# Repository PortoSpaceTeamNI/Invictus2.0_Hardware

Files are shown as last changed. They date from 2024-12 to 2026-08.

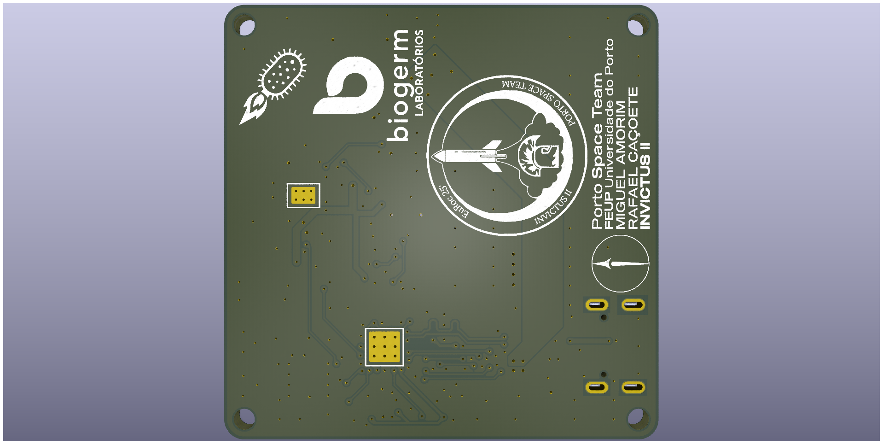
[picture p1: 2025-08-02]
Boards/PayLoad/PocketSat/Renders/PocketSat_Back.png

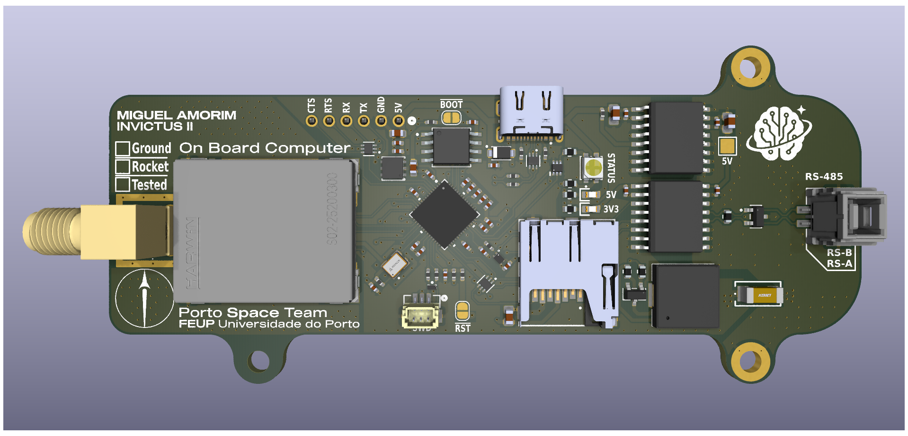
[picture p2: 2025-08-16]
Boards/Rocket Systems/OBC/Renders/OBC_front.png

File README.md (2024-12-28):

Este repositório é usado para gerir as versões dos projetos KiCAD do sistema de Avionics da Porto Space Team.
Está dividido em 2 secções: 
  1. A biblioteca de símbolos, footprints e modelos 3D dos diversos componentes usados no design, cada pasta do símbolo deve apenas incluir os ficheiros de .kicad_sym, .kicad_mod e .step todos juntos apenas dentro de uma única pasta com um nome adequado.
  2. A pasta Boards que contém os diversos ficheiros de schematic (.kicad_sch), pcb (.kicad_pcb) e project (.kicad_pro) de todo o sistema de Avionics.

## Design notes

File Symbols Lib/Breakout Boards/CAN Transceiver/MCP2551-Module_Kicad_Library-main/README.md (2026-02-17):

# MCP2551-Module-3D-model
3D model of the MCP2551 module that can be used for Kicad or any other ECad that use as .step file for rendering the 3D view

## Image

Render Canbus

## Italiano
Questo modello 3D rappresenta il modulo CanBus che sfrutta il chip MCP2551.
È stato creato per poter essere inserito negli schematici di Kicad per poterlo visualizzare nella visualizzazione 3D.
Questo modello è stato utilizzato sopratutto per la creazione delle schede che serviranno a gestire la telemetria del veicolo fatto dal team di Formula Sae dell'Unipg Racing Team

## English
This 3D model represents the CanBus module that uses the MCP2551 chip.
It was created to be inserted into the Kicad schematics to be able to view it in 3D view.
This model was used above all for the creation of the boards that will be used to manage the telemetry of the vehicle made by the Formula Sae team of the Unipg Racing Team

## Contacts 
Personal Instagram: [@marco.dok](https://www.instagram.com/marco.dok/)
Unipg Racing Team: [@unipgracing_team](https://www.instagram.com/unipgracing_team/)

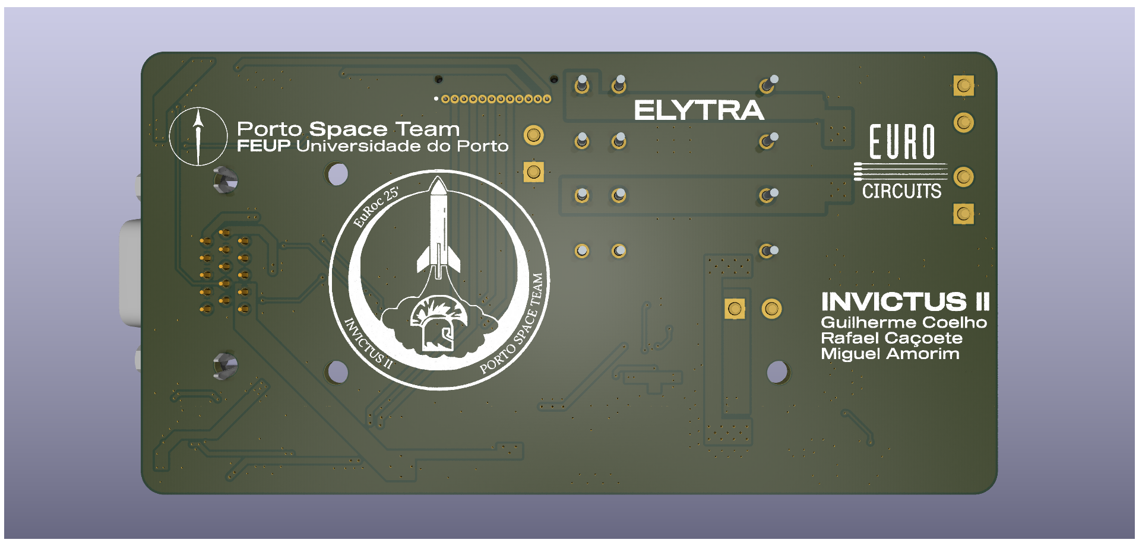
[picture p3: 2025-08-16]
Boards/Rocket Systems/Elytra/Renders/Elytra_back.png

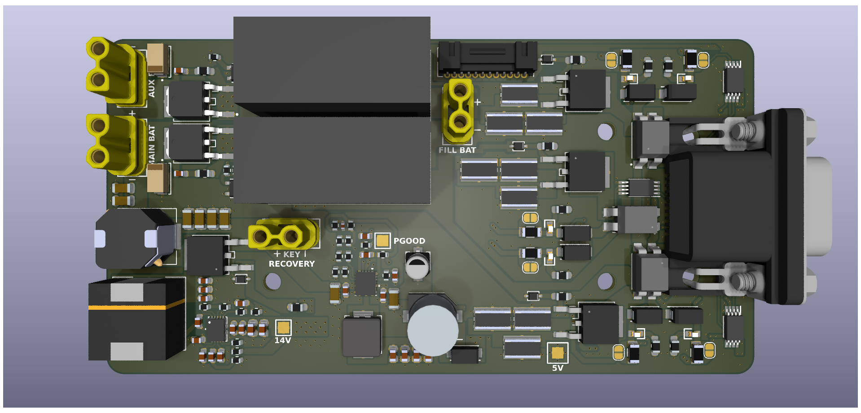
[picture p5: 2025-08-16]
Boards/Rocket Systems/Elytra/Renders/Elytra_front.png

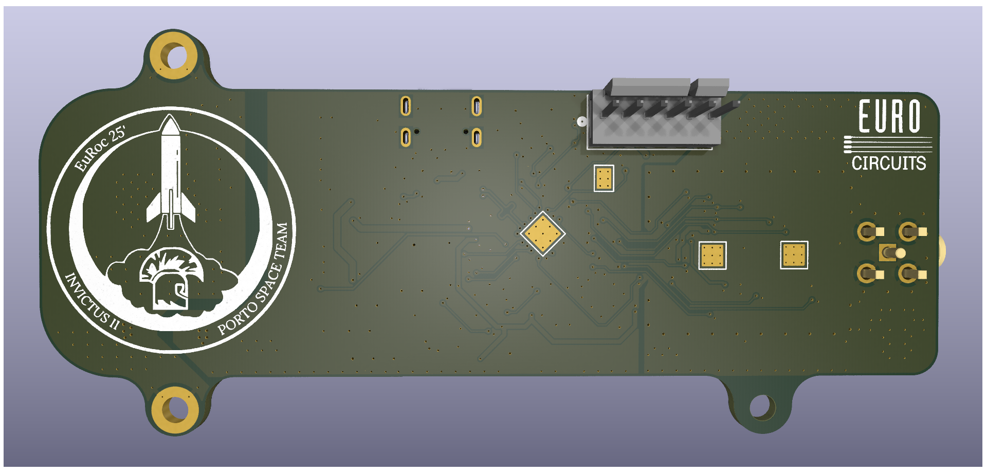
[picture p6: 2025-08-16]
Boards/Rocket Systems/OBC/Renders/OBC_back.png

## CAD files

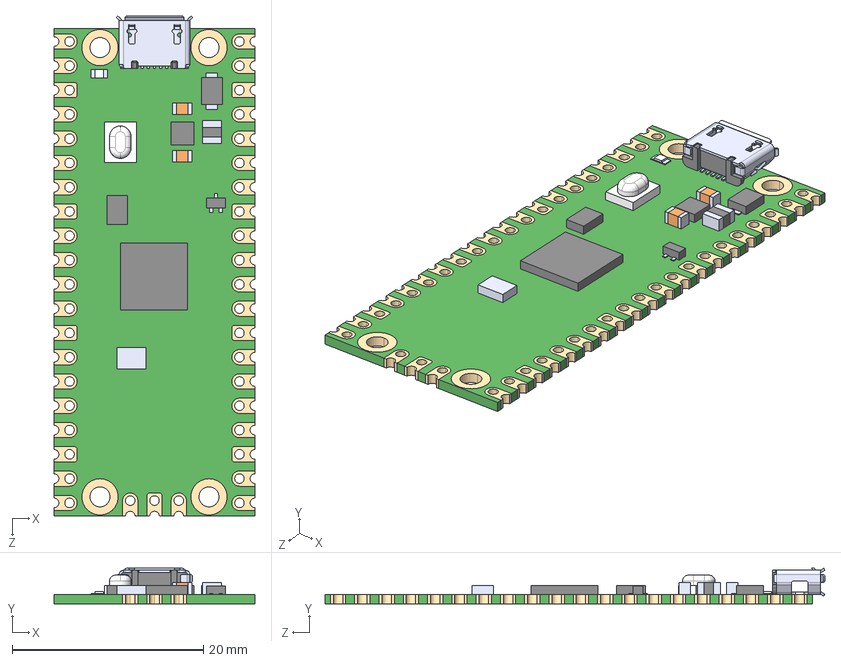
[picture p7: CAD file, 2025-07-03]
Boards/Breakout Boards/módulos/SC0915 (RP2040)/SC0915.step
21.0 x 3.73 x 52.3 mm

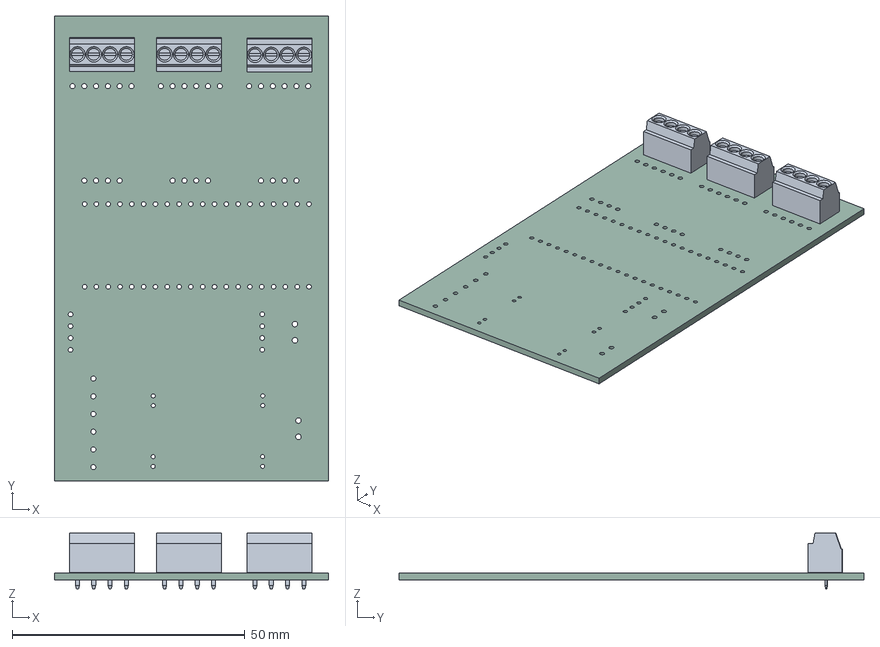
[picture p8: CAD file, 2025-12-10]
Boards/LIFT/LIFT.step
59.0 x 100.0 x 12.0 mm
LIFT_PCB

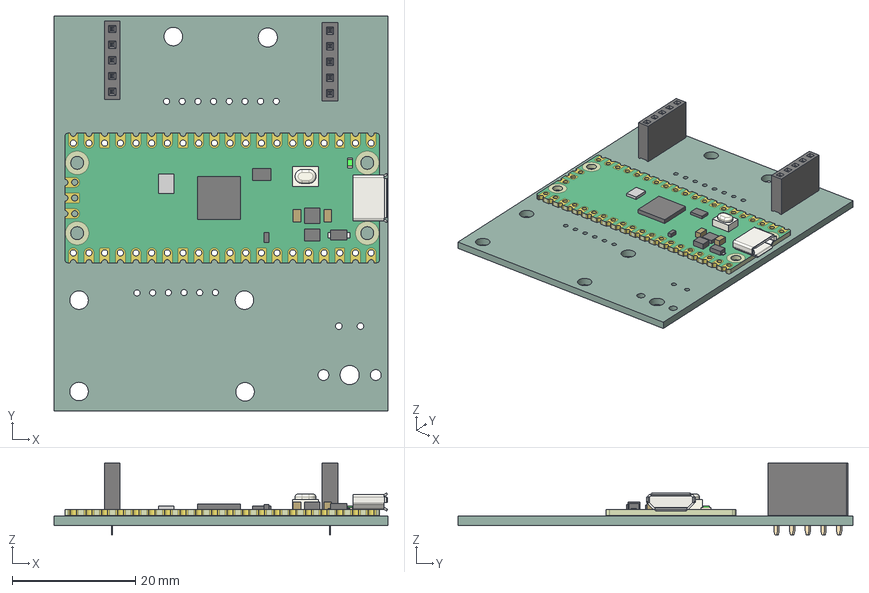
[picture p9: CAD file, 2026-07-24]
Boards/Rocket Systems/GNC/GNC_board_TH/GNC.step
54.1 x 64.0 x 11.6 mm
PinSocket_1x05_P2.54mm_Vertical x 2
RaspberryPi_Pico_Module_KiCad
GNC_board_TH_PCB

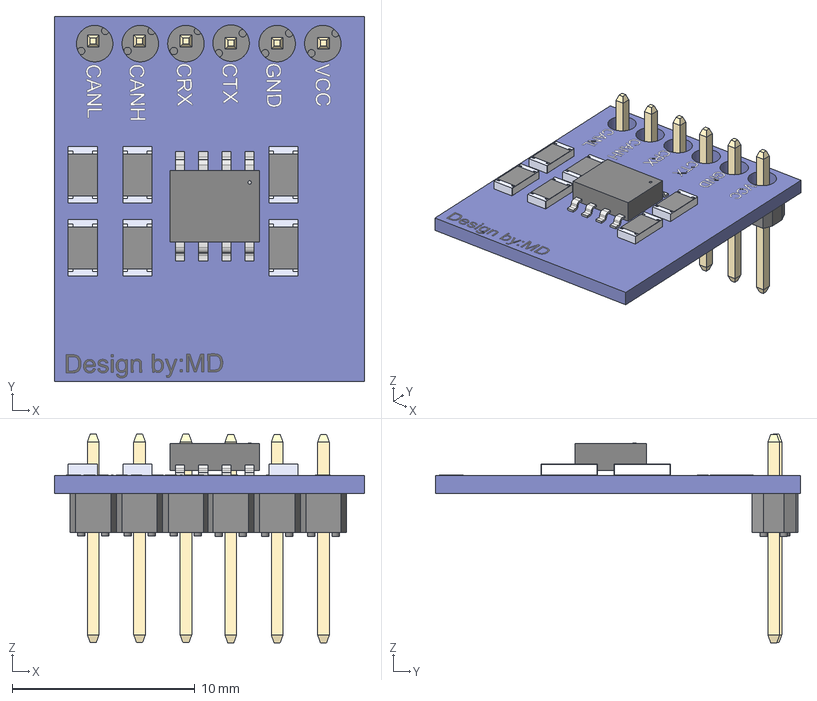
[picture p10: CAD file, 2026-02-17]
Symbols Lib/Breakout Boards/CAN Transceiver/MCP2551-Module_Kicad_Library-main/Modulo Can v10.step
17.0 x 20.0 x 11.4 mm
product
SR1206KR-07100RL x 6
68000 gold body_03 x 2
pin^68000 Gold x 6

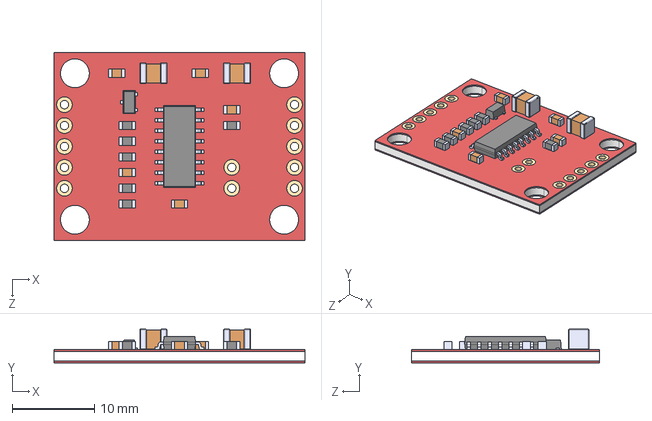
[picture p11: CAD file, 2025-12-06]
Symbols Lib/Breakout Boards/SEN-13879/SEN-13879.step
30.5 x 4.10 x 22.9 mm

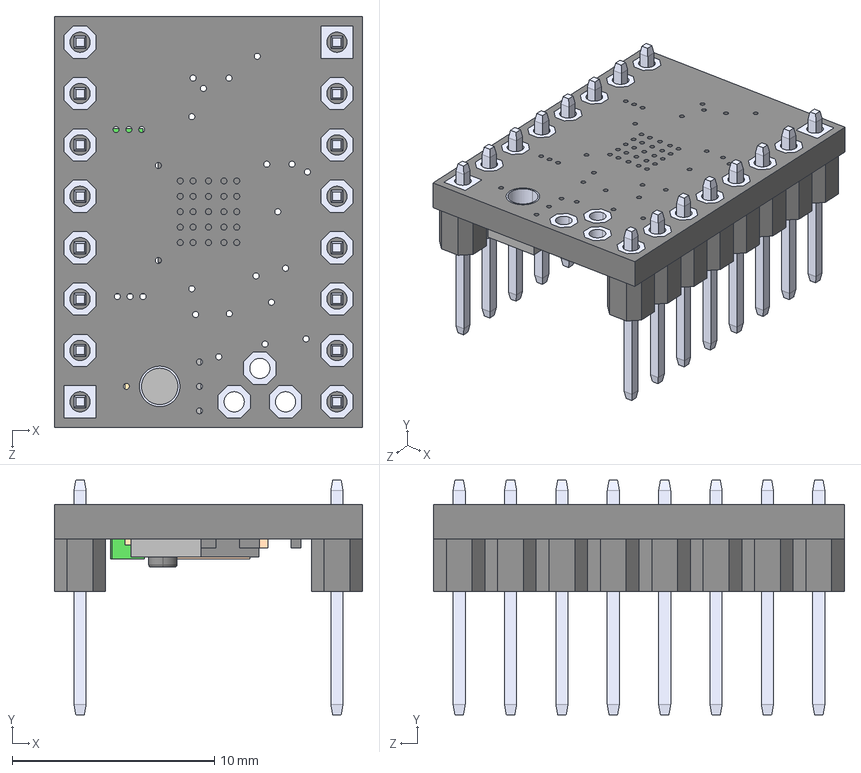
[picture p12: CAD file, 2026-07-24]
Symbols Lib/Breakout Boards/TMC2209/TMC2209_SILENTSTEPSTICK.step
15.2 x 11.6 x 20.3 mm

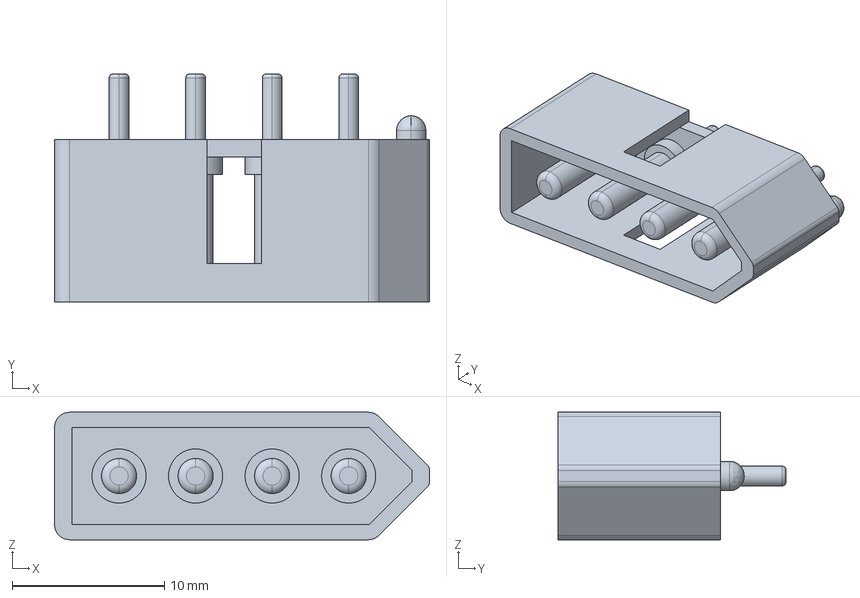
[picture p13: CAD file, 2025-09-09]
Symbols Lib/Contacts&Switches/10-18-1041/10-18-1041.stp
24.6 x 15.0 x 8.38 mm

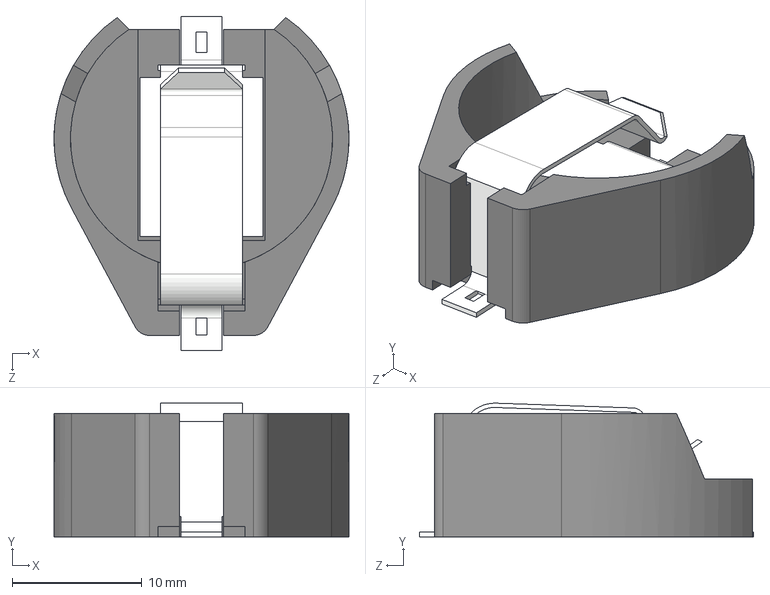
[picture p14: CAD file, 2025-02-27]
Symbols Lib/Contacts&Switches/1062TR/1062TR.step
22.8 x 10.3 x 25.8 mm

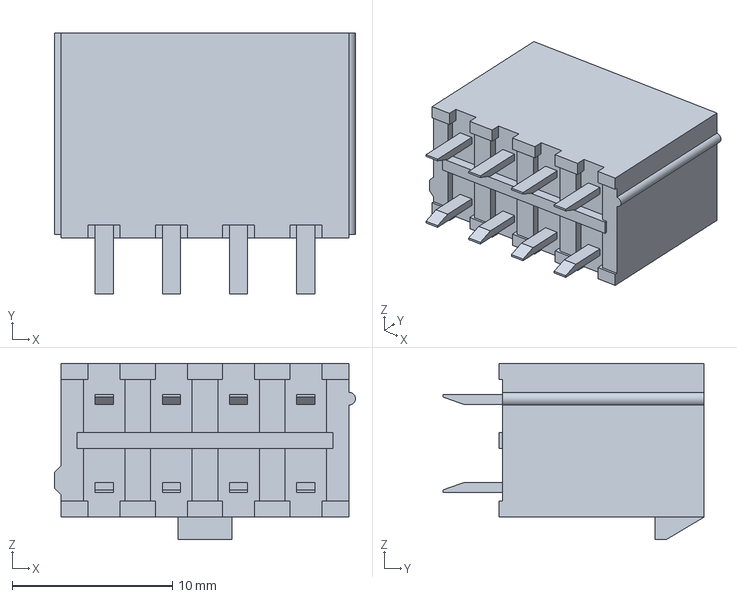
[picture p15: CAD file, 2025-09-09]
Symbols Lib/Contacts&Switches/39-28-8080/39-28-8080.stp
18.8 x 16.3 x 11.0 mm

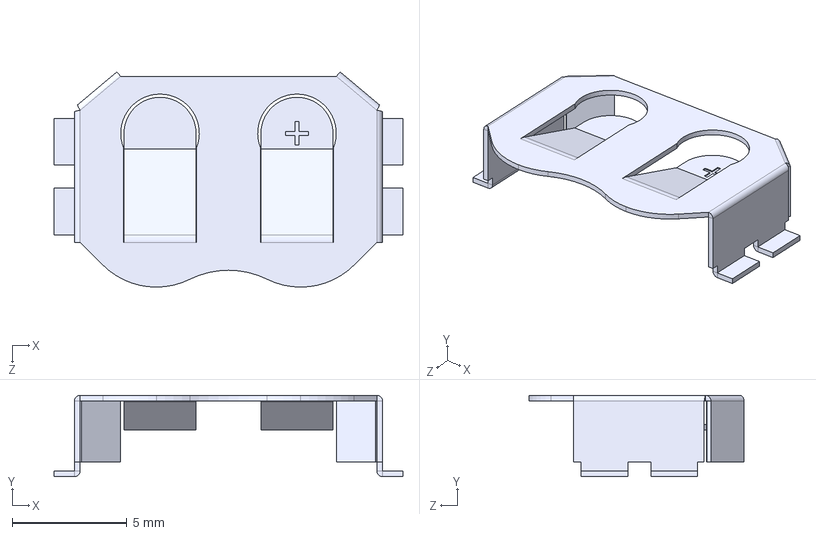
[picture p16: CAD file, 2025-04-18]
Symbols Lib/Contacts&Switches/BAT_HLD_012/BAT-HLD-012-SMT-TR.step
15.2 x 3.56 x 9.40 mm

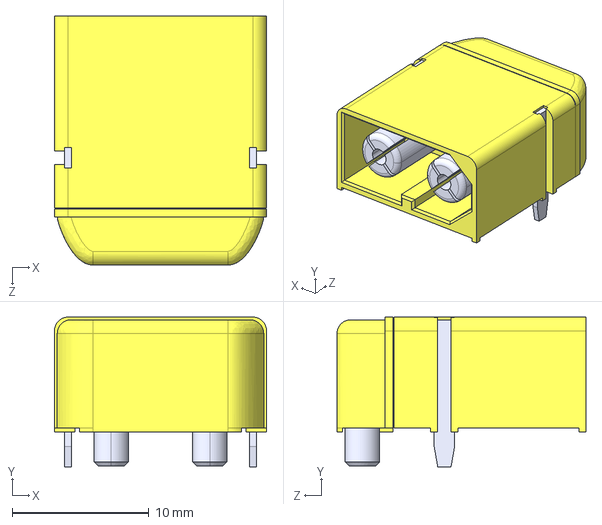
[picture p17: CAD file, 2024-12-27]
Symbols Lib/Contacts&Switches/Conn XT60PW-M/XT60PW-M.step
15.5 x 11.0 x 18.2 mm

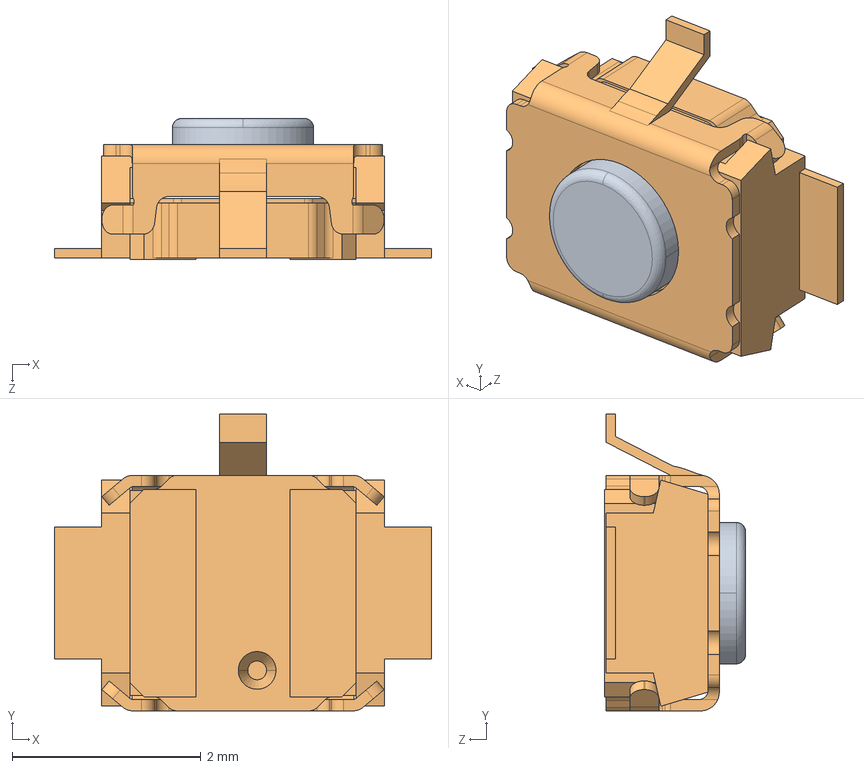
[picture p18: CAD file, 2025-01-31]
Symbols Lib/Contacts&Switches/E-Switch_Small/TL1017AABF160QG.stp
4.00 x 3.15 x 1.50 mm

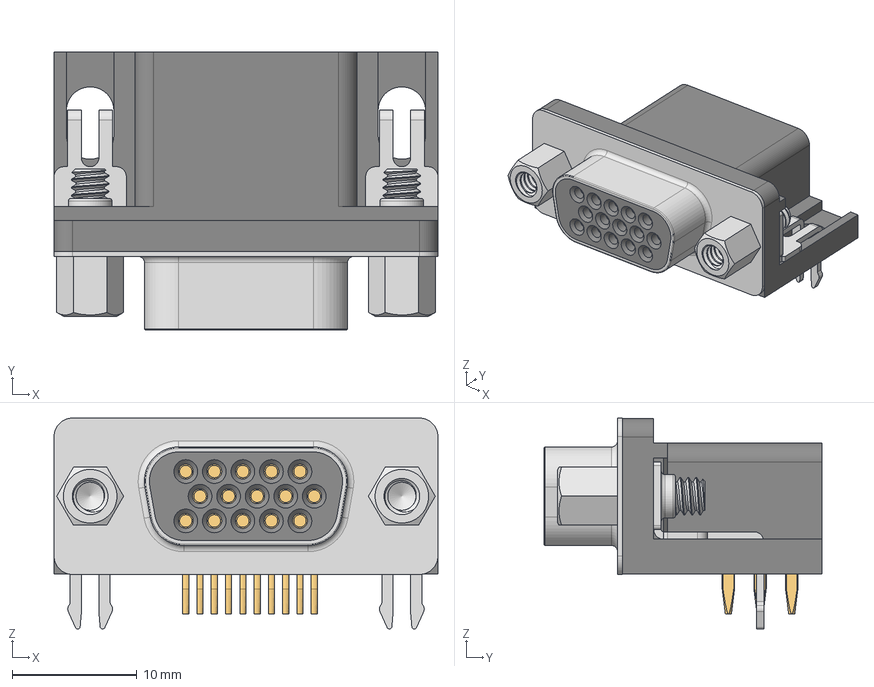
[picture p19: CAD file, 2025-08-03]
Symbols Lib/Contacts&Switches/HDL15-SL-B/VGA-DB15F.stp
30.8 x 22.3 x 16.9 mm
VGA-2H
VGA-1H
VGA-3 x 2
VGA-4H-1 x 5
VGA-4H-2 x 5
VGA-4H-3 x 5
VGA-5
VGA-6 x 2

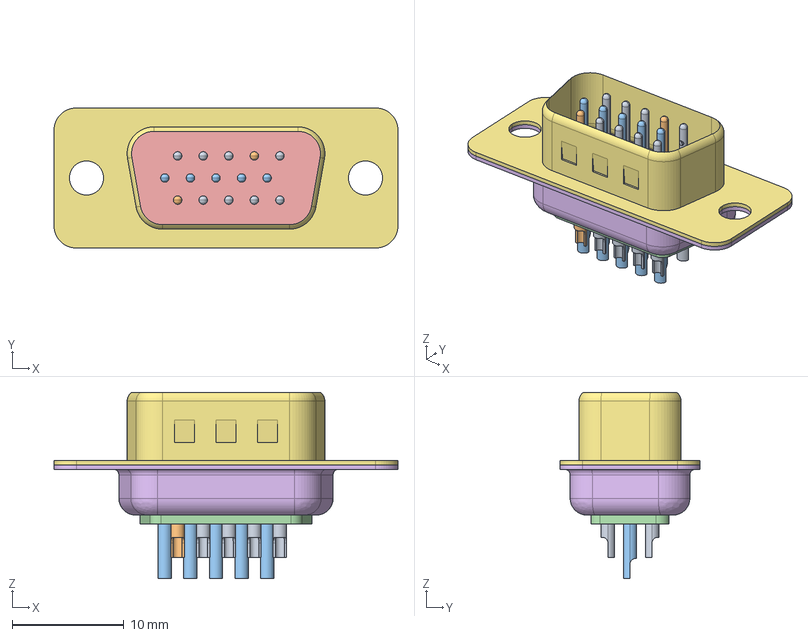
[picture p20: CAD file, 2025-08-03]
Symbols Lib/Contacts&Switches/MaleVGA/MaleVGA.stp
30.8 x 12.6 x 16.7 mm
MSBR-19
MSBR-18
MSBR-17
MSBR-16
MSBR-15
MSBR-14
MSBR-13
MSBR-12
MSBR-11
MSBR-10
MSBR-9
MSBR-8
MSBR-7
MSBR-6
MSBR-5
MSBR-4
MSBR-3
MSBR-2
MSBR-1

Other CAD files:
Symbols Lib/Contacts&Switches/PCB.RPSMAFRA.HT/PCB.RPSMAFRA.HT.stp
Symbols Lib/Contacts&Switches/PR12-12V-360-1C/PR12-12V-360-1C.step
Symbols Lib/Contacts&Switches/PR30-12V-450-1C-E/PR30-12V-450-1C-E.step
Symbols Lib/Contacts&Switches/RFI Shield/s02-25200300.stp
Symbols Lib/Contacts&Switches/1722981104/172298-1104.stp
Symbols Lib/Contacts&Switches/1723103102/1723103102.step
Symbols Lib/Contacts&Switches/1723103103/1723103103.step
Symbols Lib/Contacts&Switches/1723163206/1723163206.step
Symbols Lib/Contacts&Switches/1723163304/1723163304.step
Symbols Lib/Contacts&Switches/215931-0270/2159310270.stp
Symbols Lib/Contacts&Switches/215932-0270/215932-0270.stp
Symbols Lib/Contacts&Switches/2200981271/2200981271.stp
Symbols Lib/Contacts&Switches/26013116/26013116.step
Symbols Lib/Contacts&Switches/393570004/393570004.stp
Symbols Lib/Contacts&Switches/5024430270/5024430270.stp
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

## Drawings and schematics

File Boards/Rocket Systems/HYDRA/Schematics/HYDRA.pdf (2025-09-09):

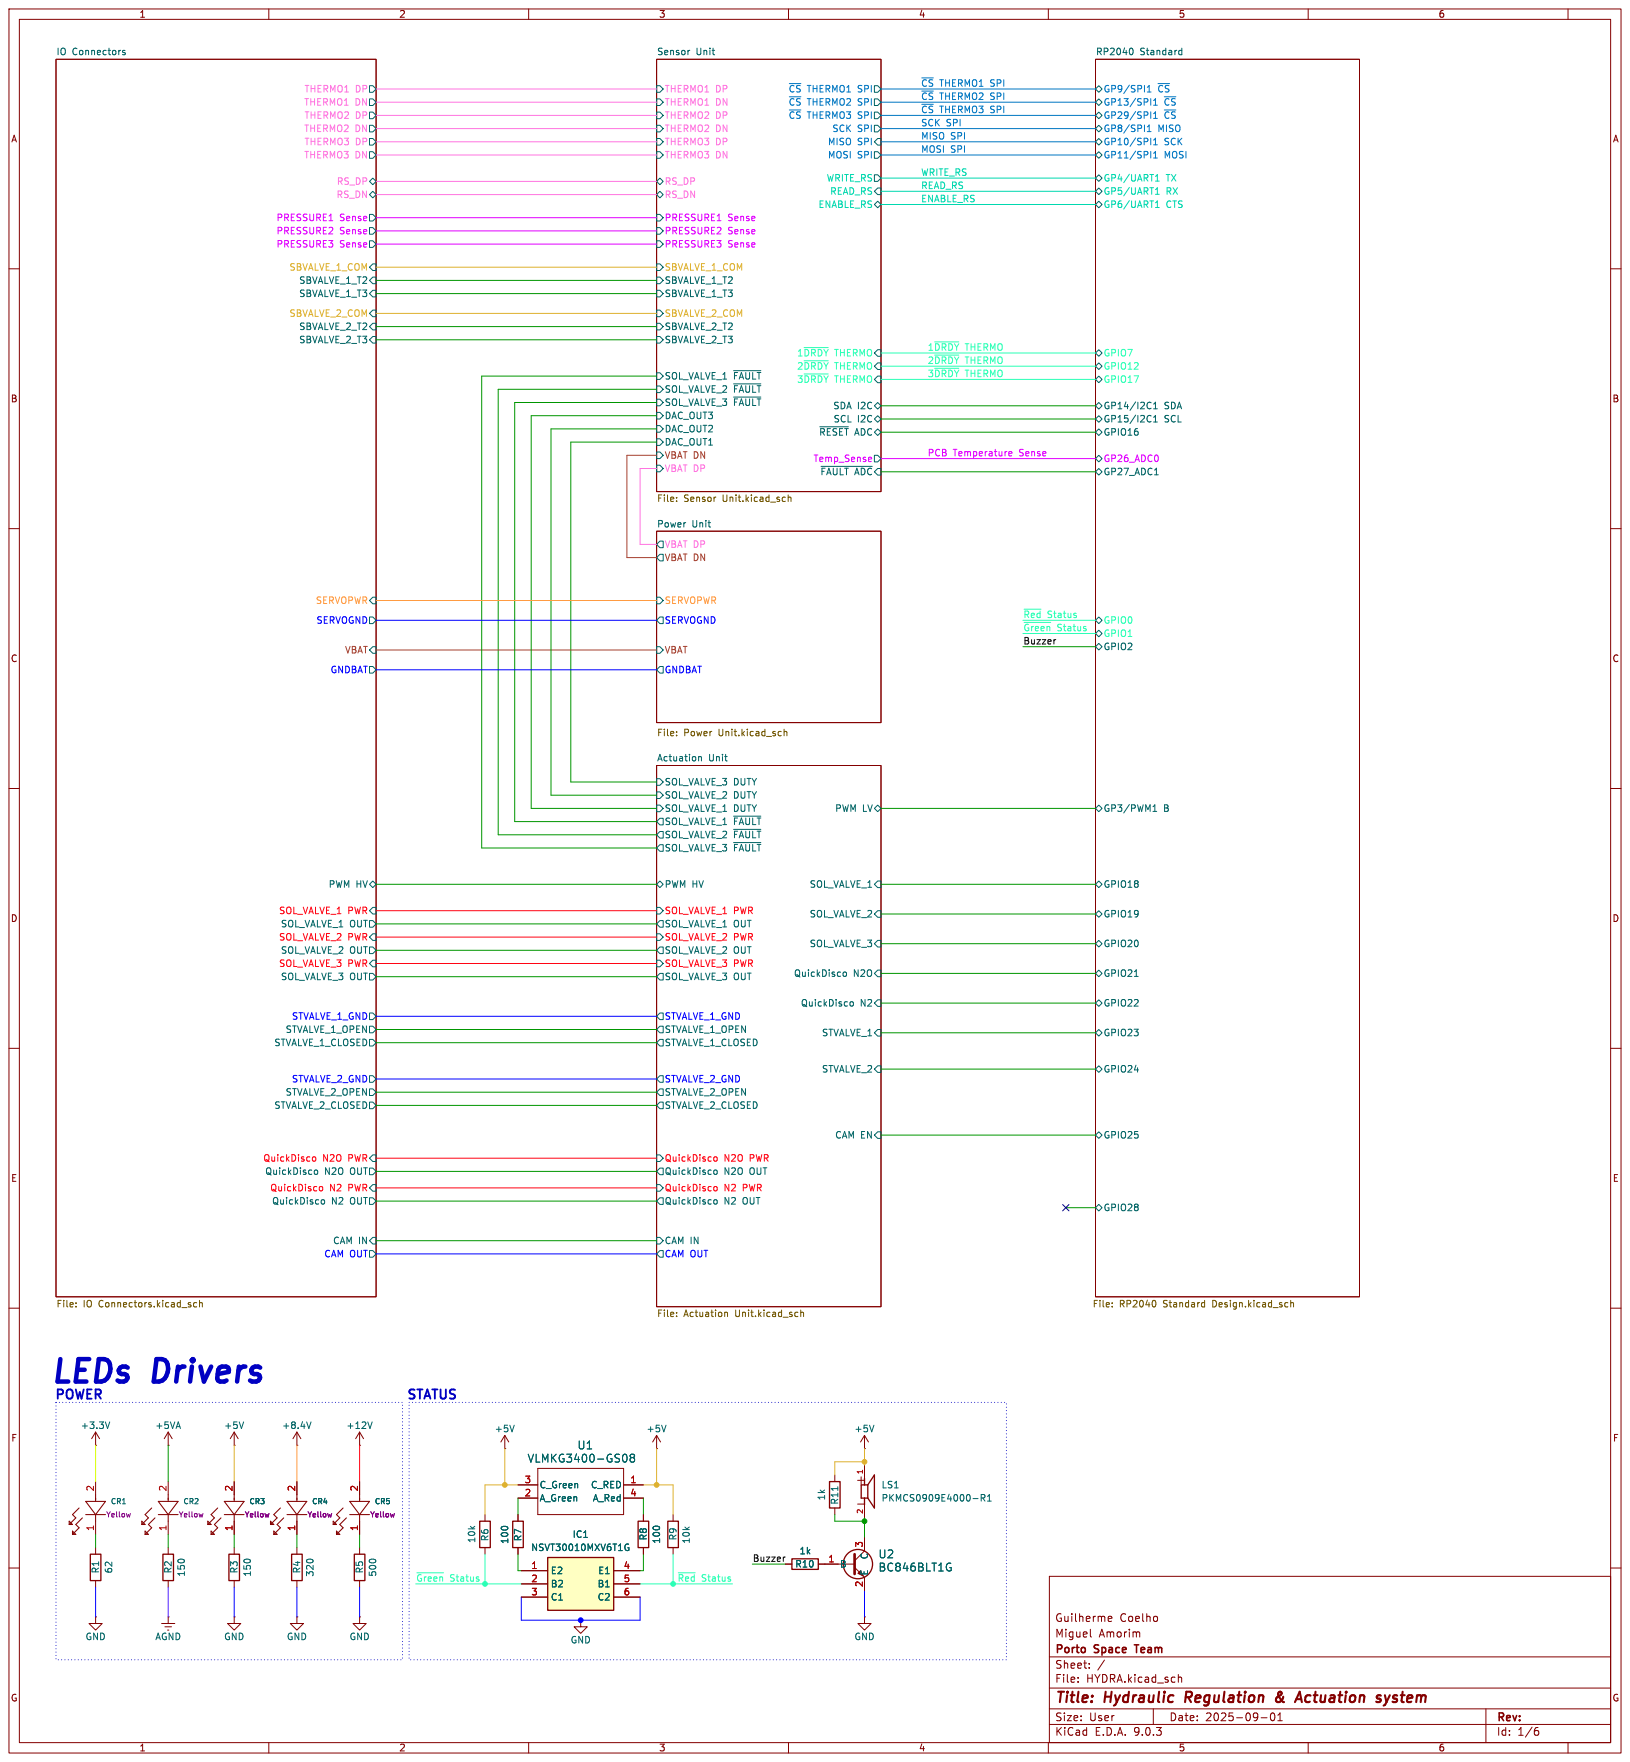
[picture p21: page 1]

SCK SPI 1~{DRDY}THERMO
~{Green}Status Buzzer WRITE_RS
SBVALVE_2_T2 SBVALVE_2_T3 SOL_VALVE_1 ~{FAULT} SOL_VALVE_2 ~{FAULT} SOL_VALVE_3 ~{FAULT} DAC_OUT1 RS_DP RS_DN

RP2040 Standard
~{CS}THERMO2 SPI ~{CS}THERMO3 SPI MISO SPI SCK SPI ~{CS}THERMO1 SPI 1~{DRDY}THERMO

~{CS}THERMO1 SPI THERMO3 DP
~{CS}THERMO2 SPI 3~{DRDY}THERMO MOSI SPI MISO SPI ~{CS}THERMO3 SPI THERMO1 DN
THERMO2 DP
THERMO2 DN

VBAT DP
VBAT GNDBAT VBAT DN

Id: 1/6 Title: Hydraulic Regulation & Actuation system

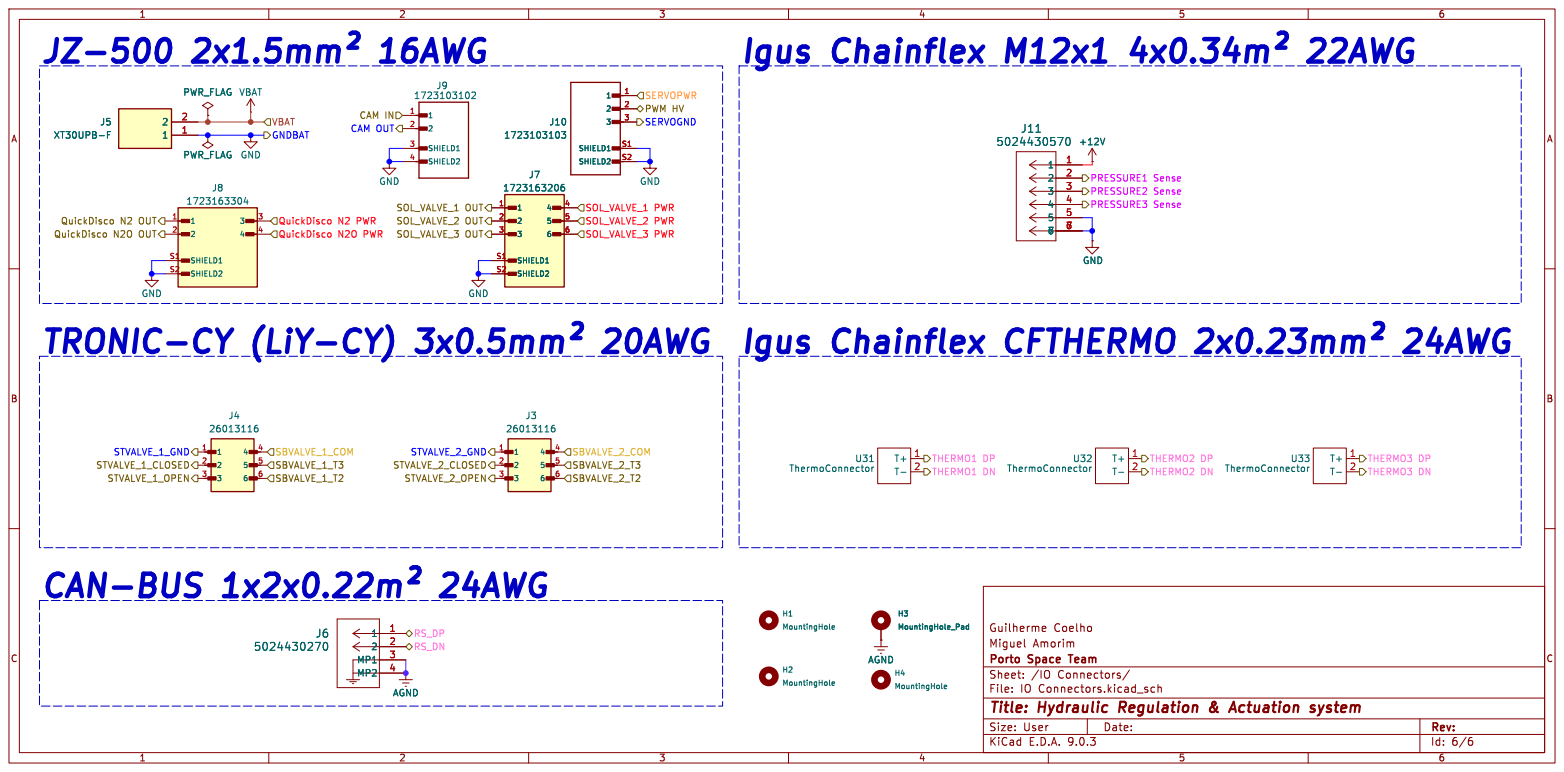
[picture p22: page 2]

Igus Chainflex CFTHERMO þÿ2x0.23mm² 24AWG

Id: 6/6 Title: Hydraulic Regulation & Actuation system

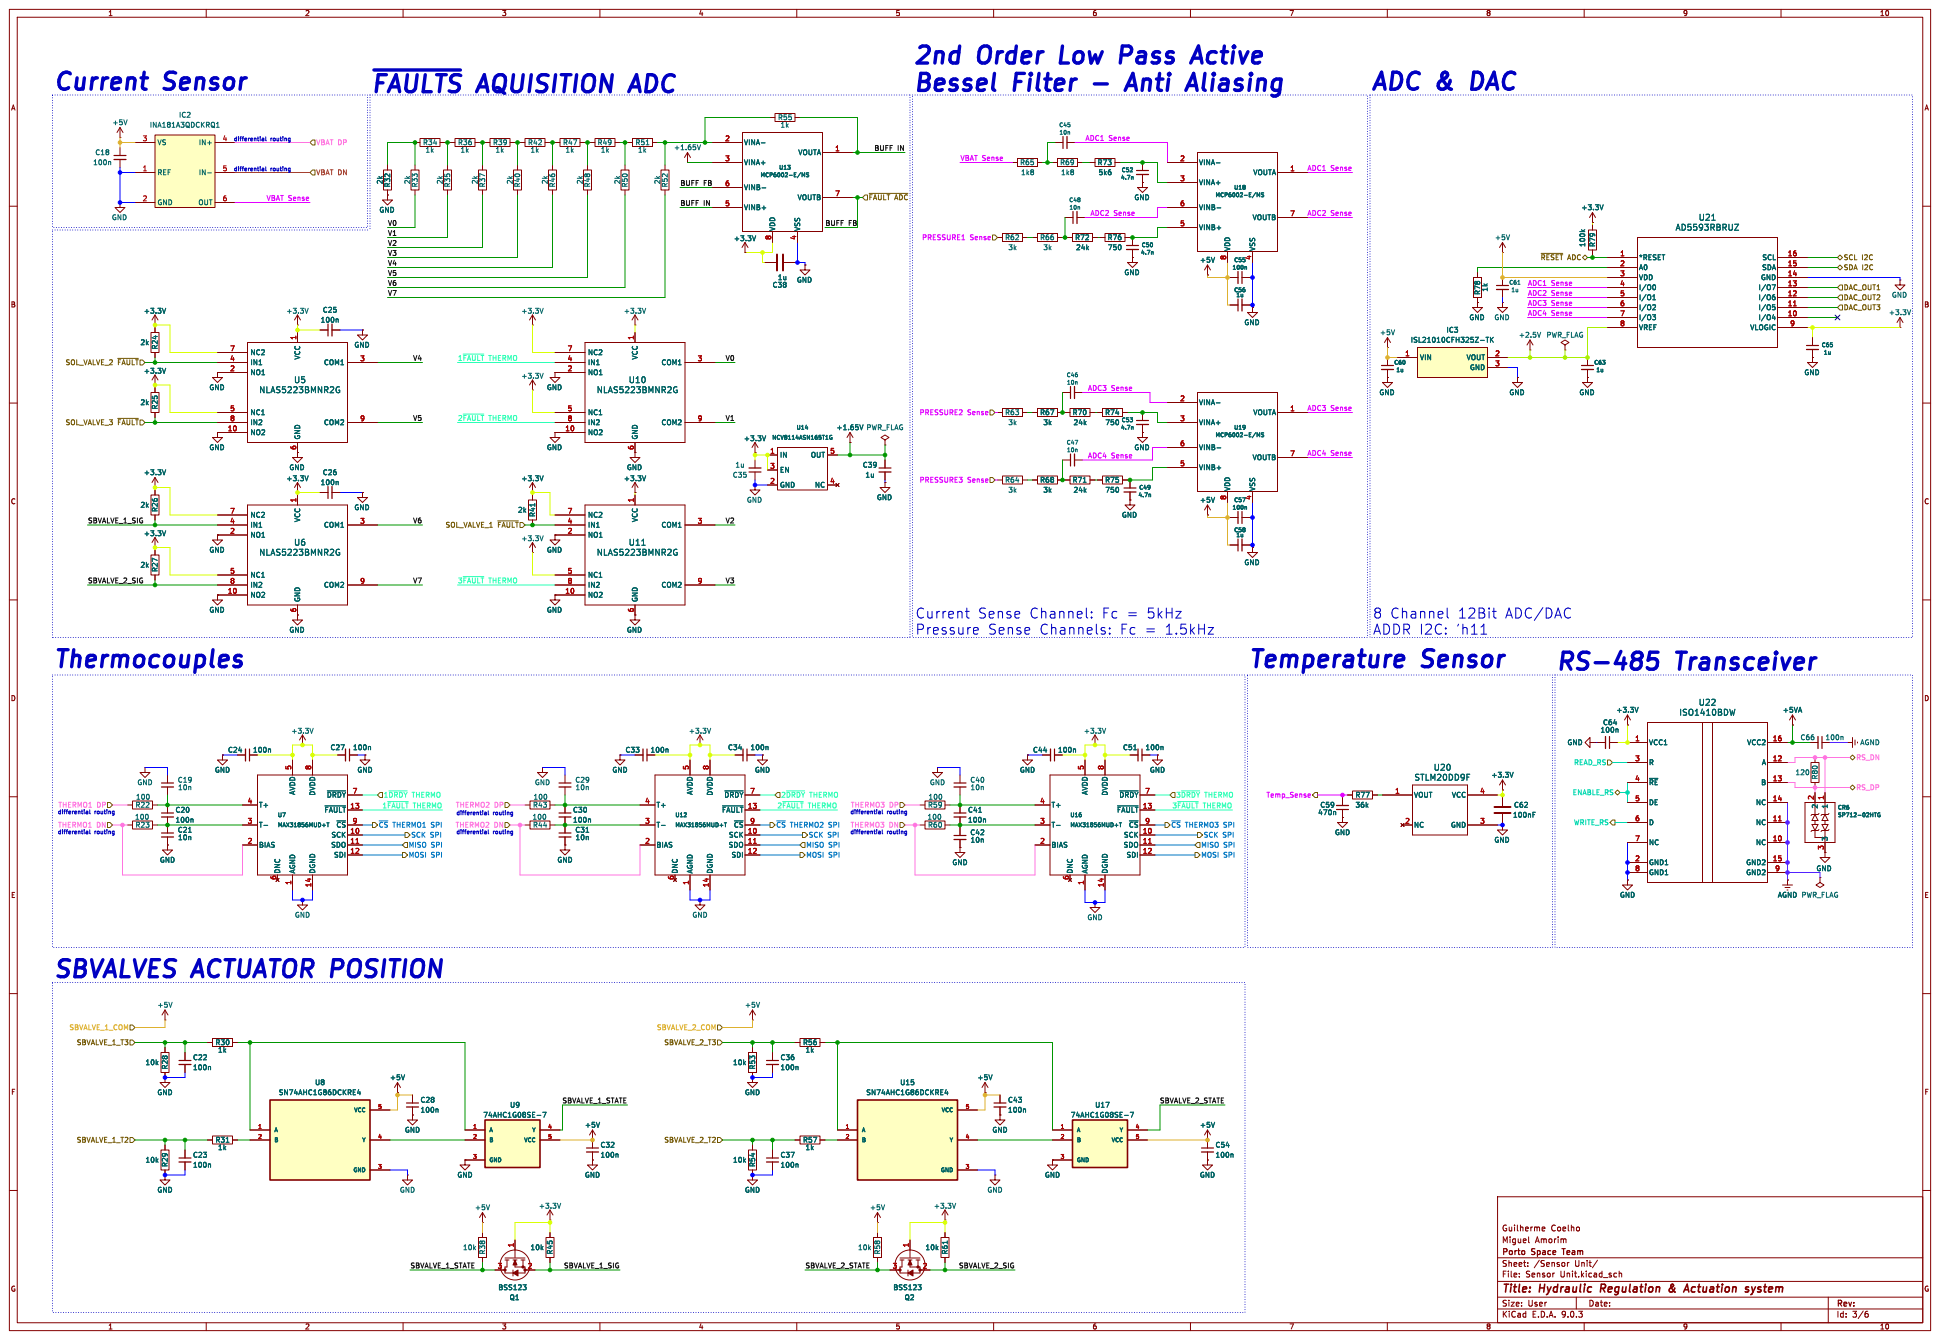
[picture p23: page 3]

2nd Order Low Pass Active
Bessel Filter - Anti Aliasing

ADC1 Sense ADC4 Sense BUFF FB

4 VOUTA 1 VOUTB 7 U18 MCP6002-E/MS GND

Current Sense Channel: Fc = 5kHz
Pressure Sense Channels: Fc = 1.5kHz

~{DRDY}7 ~{FAULT}13 ~{CS}9 SCK 10 SDO 11 SDI 12 U7 MAX31856MUD+T C20

~{DRDY}7 ~{FAULT}13 ~{CS}9 SCK 10 SDO 11 SDI 12 C20

~{DRDY}7 ~{FAULT}13 ~{CS}9 SCK 10 SDO 11 SDI 12 C31

6 AVDD
~{DRDY}7 ~{FAULT}13 ~{CS}9 SCK 10 SDO 11 SDI 12 U12 MAX31856MUD+T

~{DRDY}7 ~{FAULT}13 ~{CS}9 SCK 10 SDO 11 SDI 12 U16 MAX31856MUD+T

3~{DRDY}THERMO MISO SPI THERMO1 DN

Id: 3/6 Title: Hydraulic Regulation & Actuation system

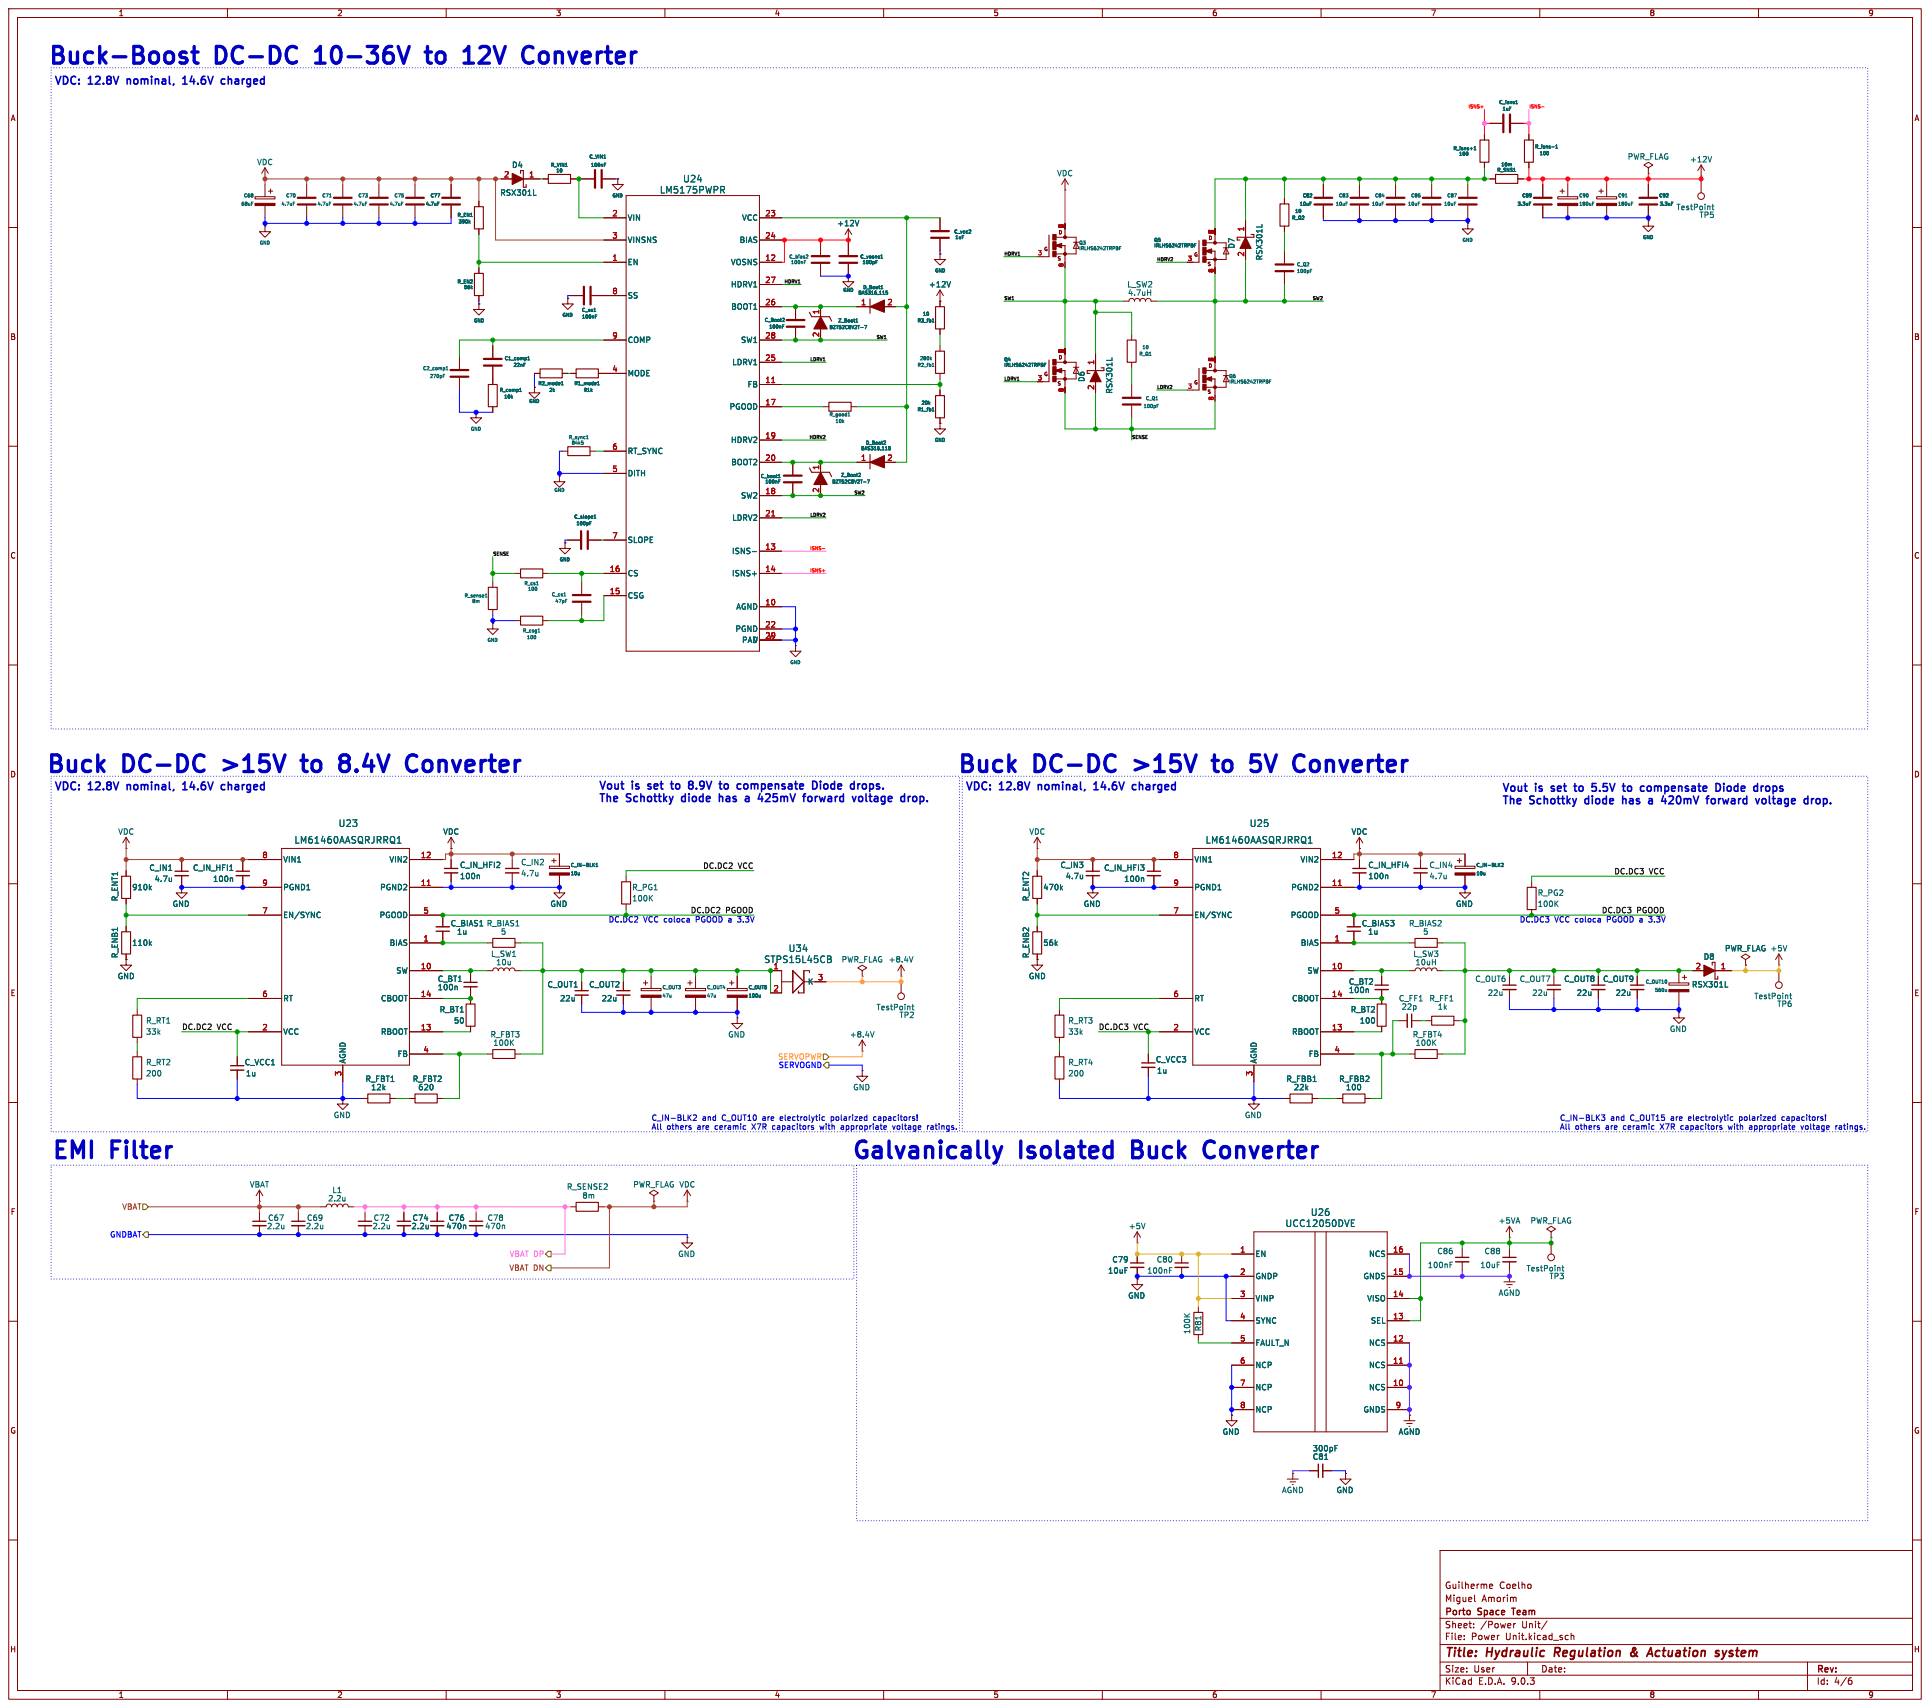
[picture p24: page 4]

Vout is set to 8.9V to compensate Diode drops.
The Schottky diode has a 425mV forward voltage drop.

Vout is set to 5.5V to compensate Diode drops
The Schottky diode has a 420mV forward voltage drop. C_OUT8

Id: 4/6 Title: Hydraulic Regulation & Actuation system

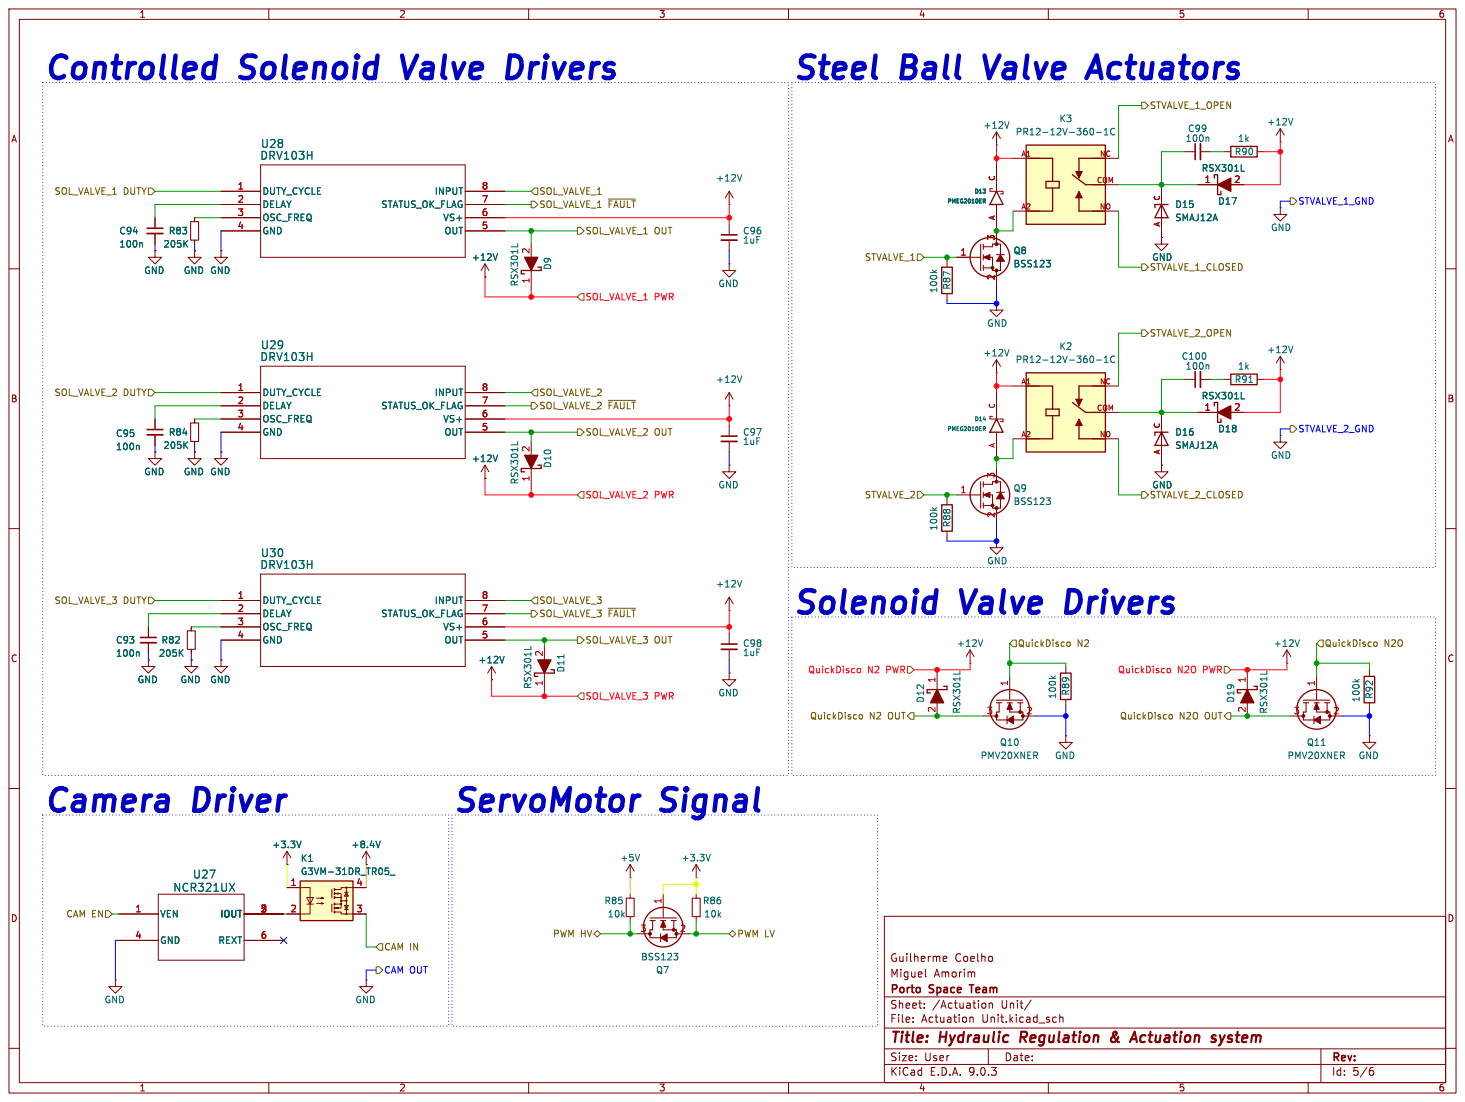
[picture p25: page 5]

PWM HV CAM IN

Id: 5/6 Title: Hydraulic Regulation & Actuation system

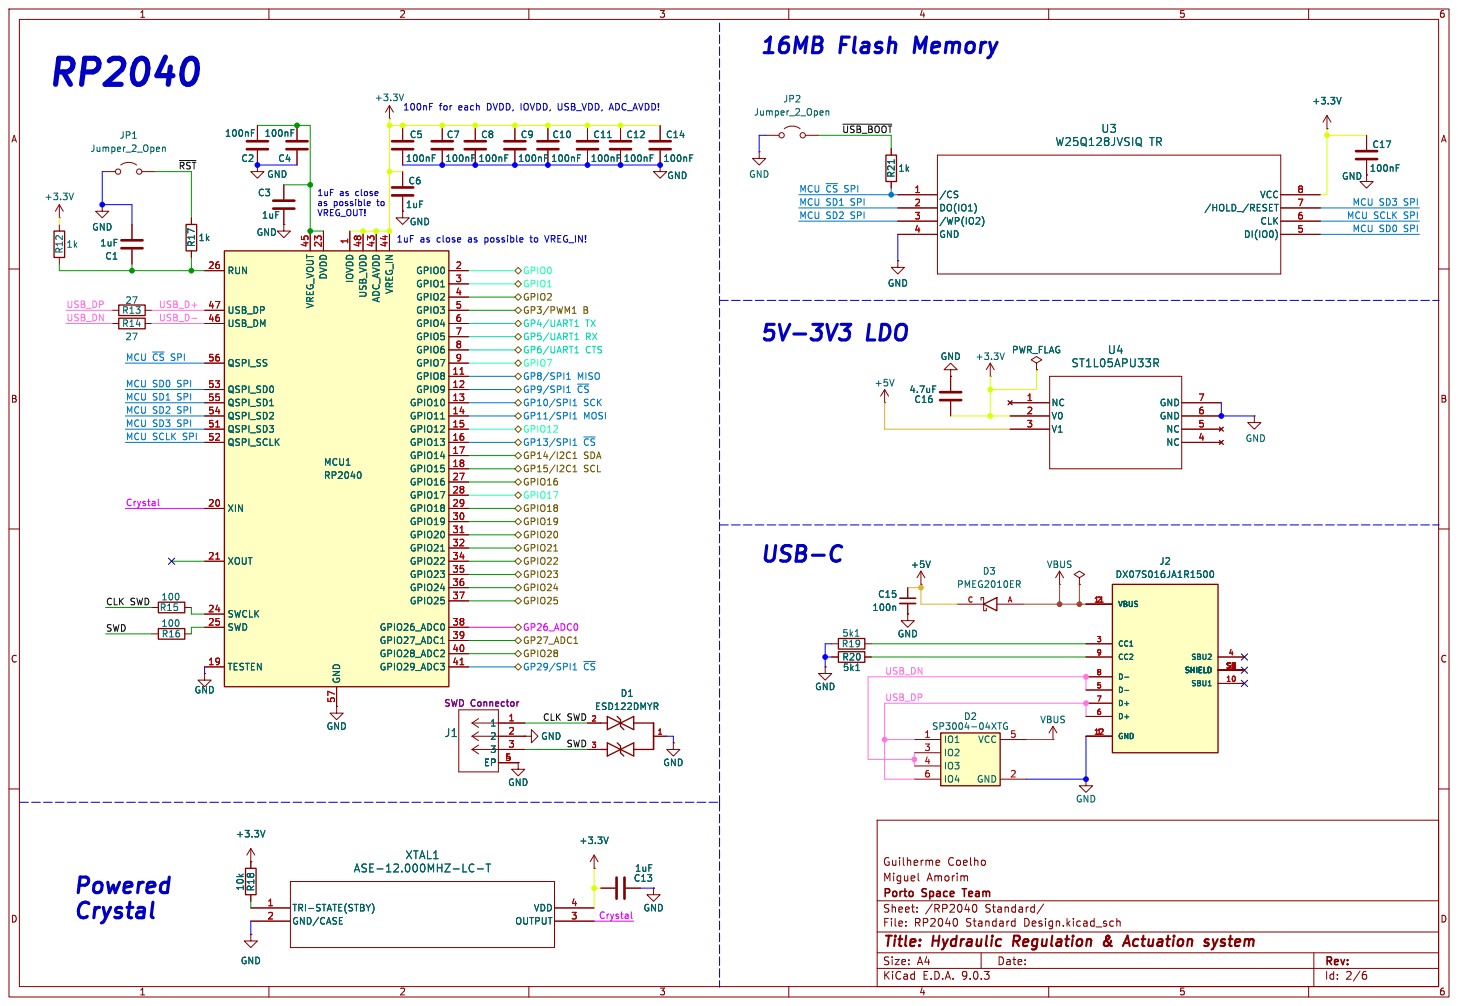
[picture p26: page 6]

Id: 2/6 Title: Hydraulic Regulation & Actuation system

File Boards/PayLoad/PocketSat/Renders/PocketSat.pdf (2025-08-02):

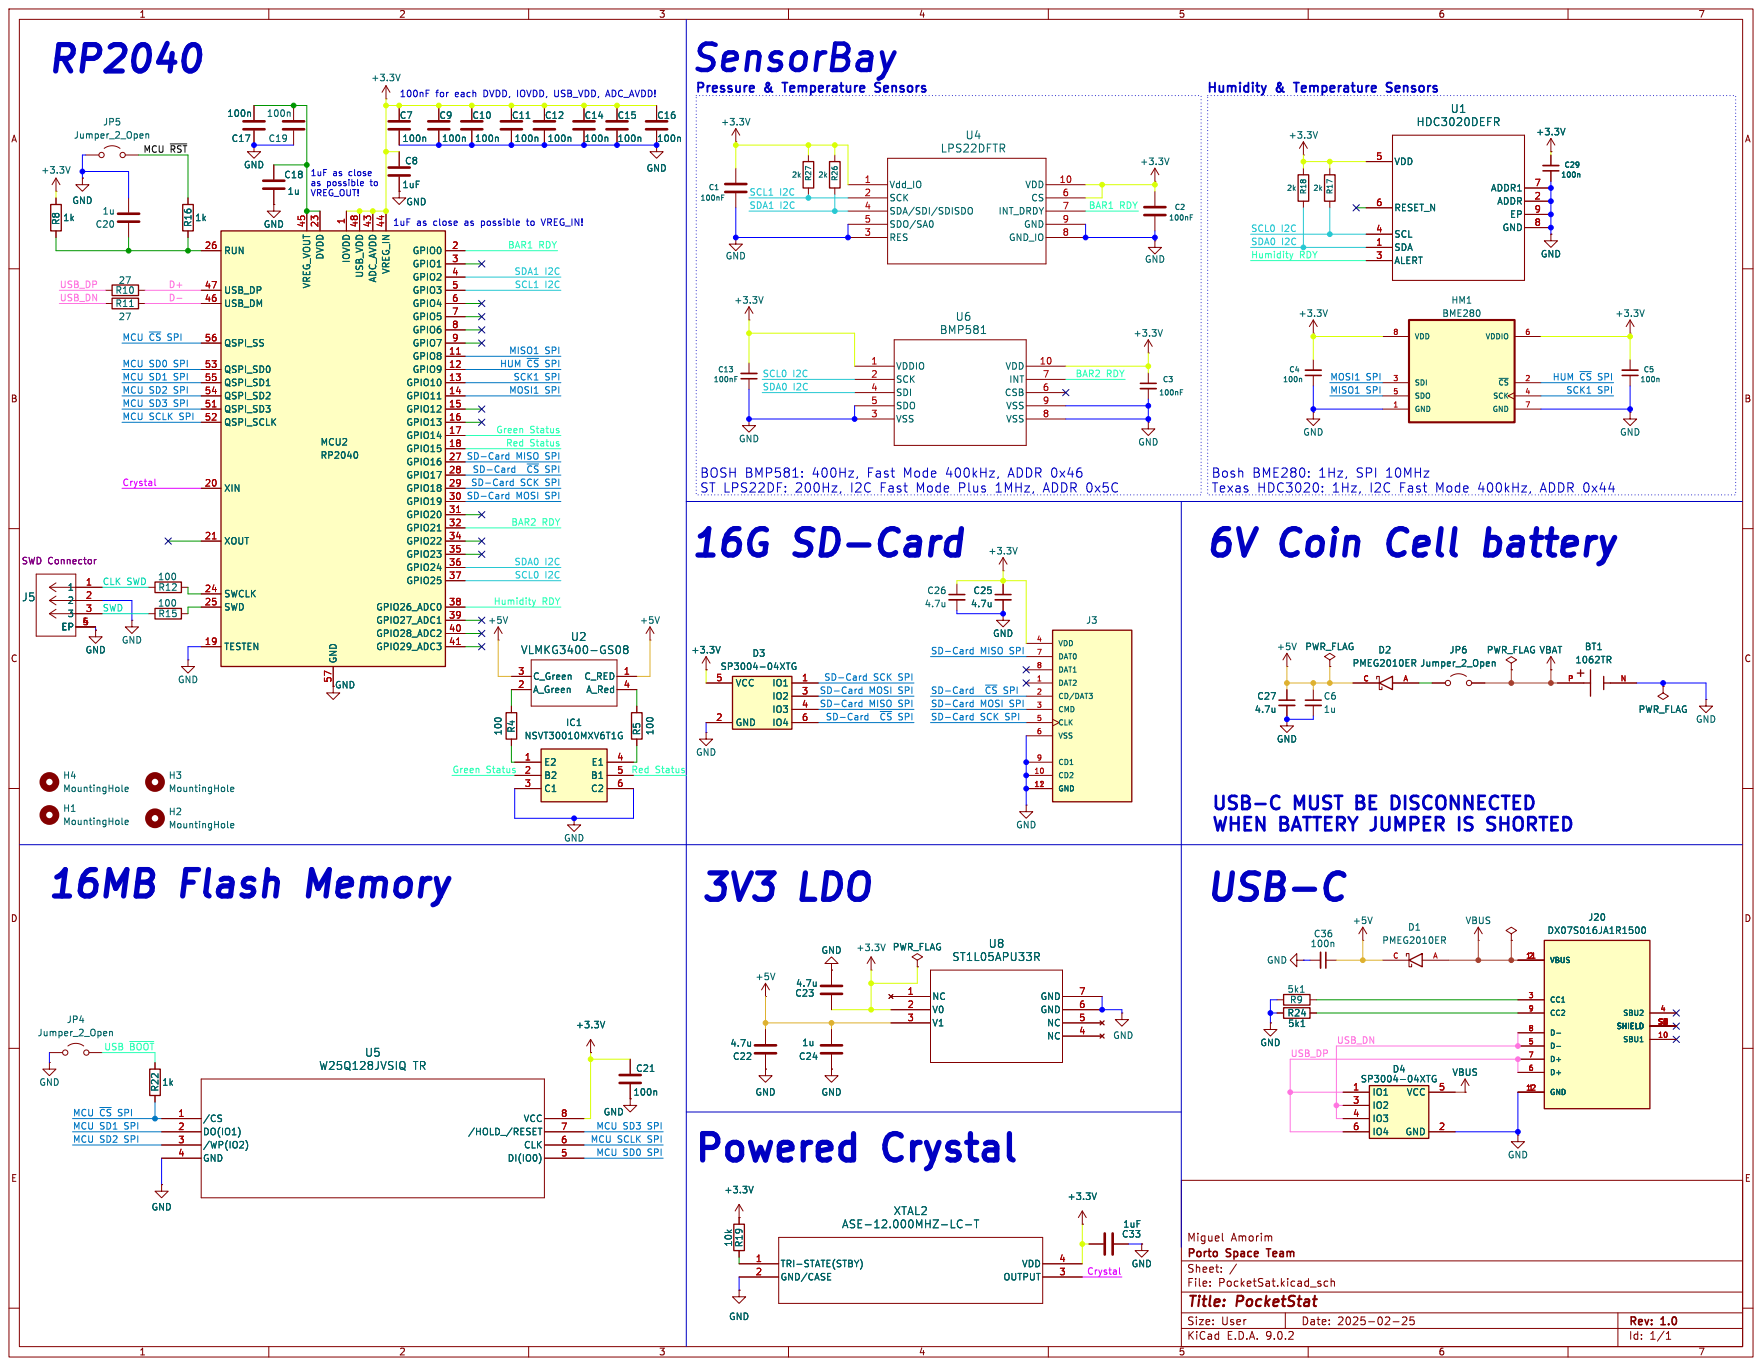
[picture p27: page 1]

Bosh BME280: 1Hz, SPI 10MHz
Texas HDC3020: 1Hz, I2C Fast Mode 400kHz, ADDR 0x44
6V Coin Cell battery

ST LPS22DF: 200Hz, I2C Fast Mode Plus 1MHz, ADDR 0x5C
16G SD-Card

WHEN BATTERY JUMPER IS SHORTED

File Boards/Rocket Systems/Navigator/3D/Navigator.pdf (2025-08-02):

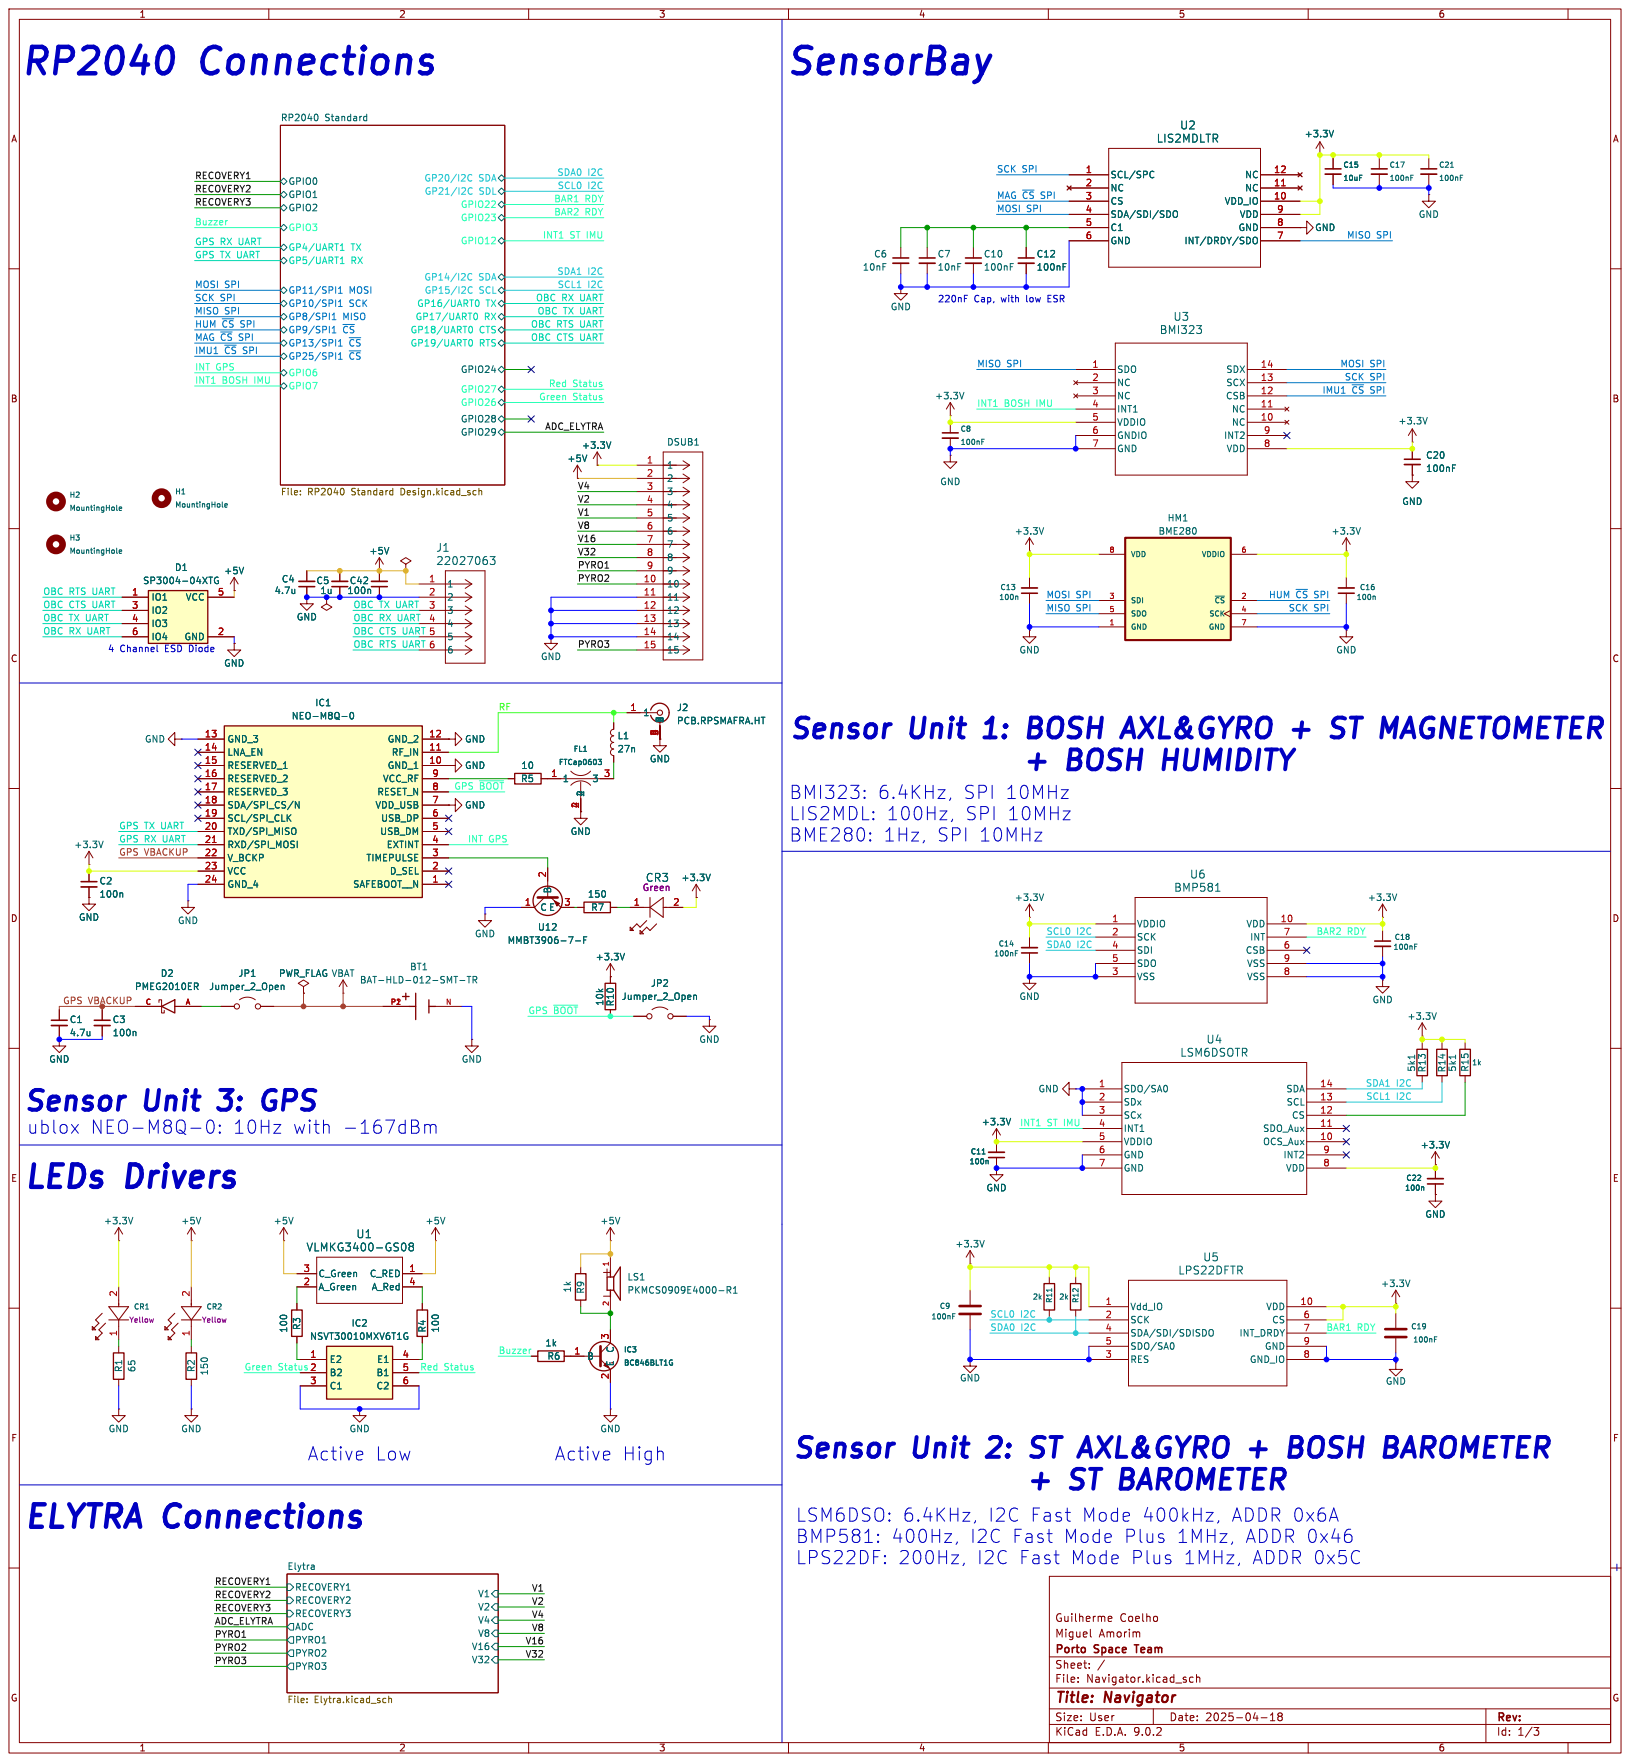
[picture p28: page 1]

10nF GND
220nF Cap, with low ESR Sensor Unit 1: BOSH AXL&GYRO + ST MAGNETOMETER

SCL1 I2C MAG ~{CS}SPI MISO SPI HUM ~{CS}SPI

IMU1 ~{CS}SPI SCK SPI V8

4 Channel ESD Diode Sensor Unit 3: GPS

Sensor Unit 2: ST AXL&GYRO + BOSH BAROMETER
LSM6DSO: 6.4KHz, I2C Fast Mode 400kHz, ADDR 0x6A
BMP581: 400Hz, I2C Fast Mode Plus 1MHz, ADDR 0x46
LPS22DF: 200Hz, I2C Fast Mode Plus 1MHz, ADDR 0x5C

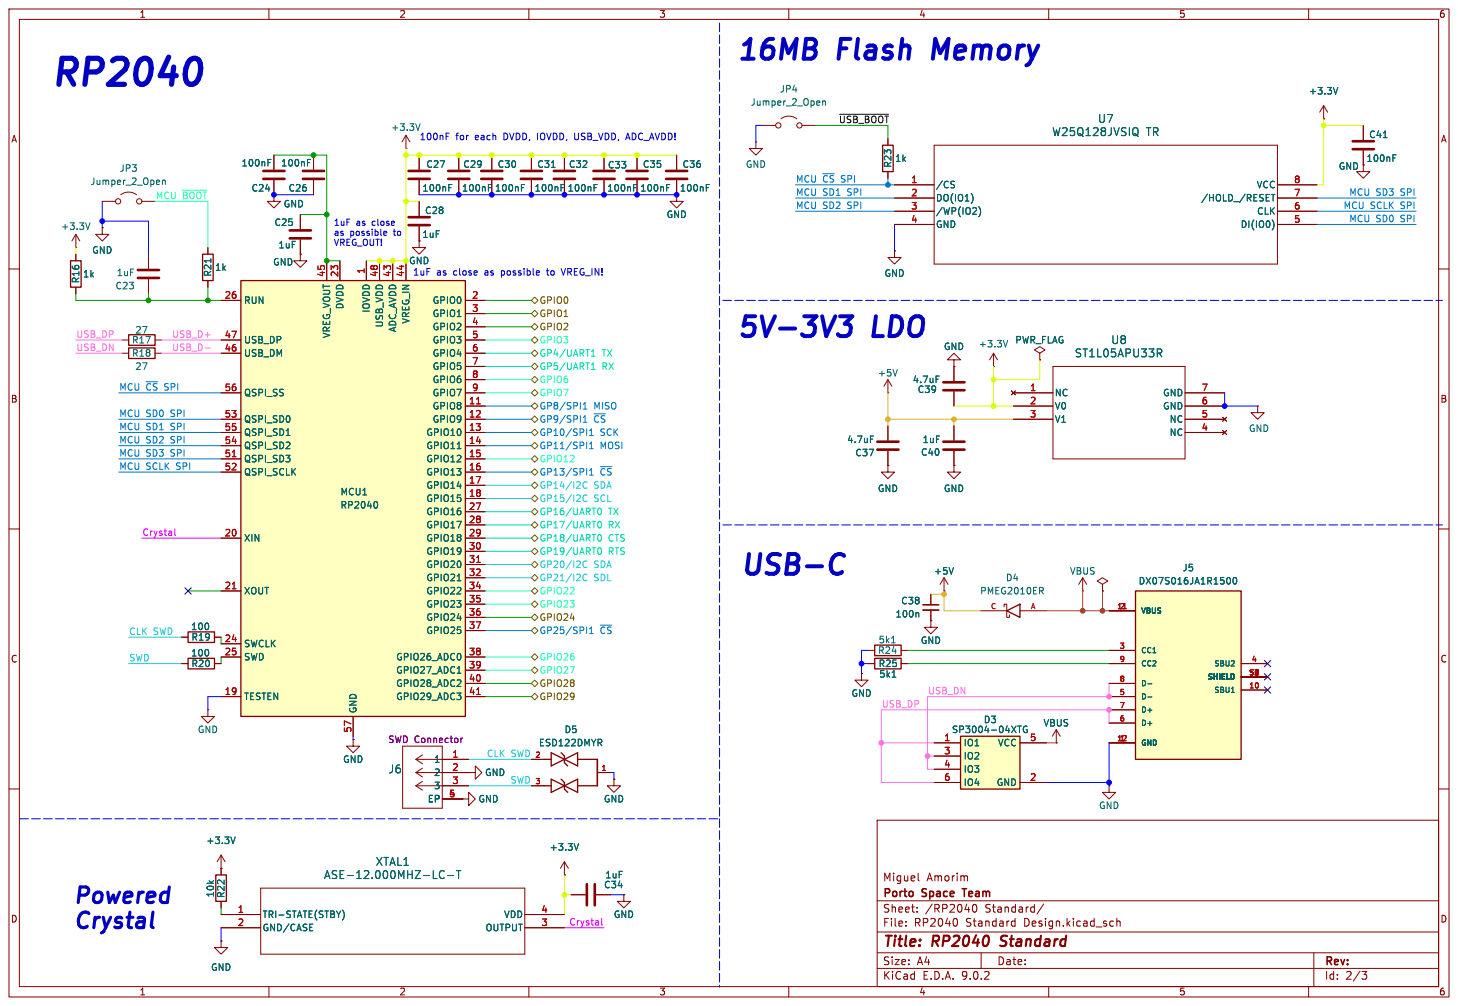
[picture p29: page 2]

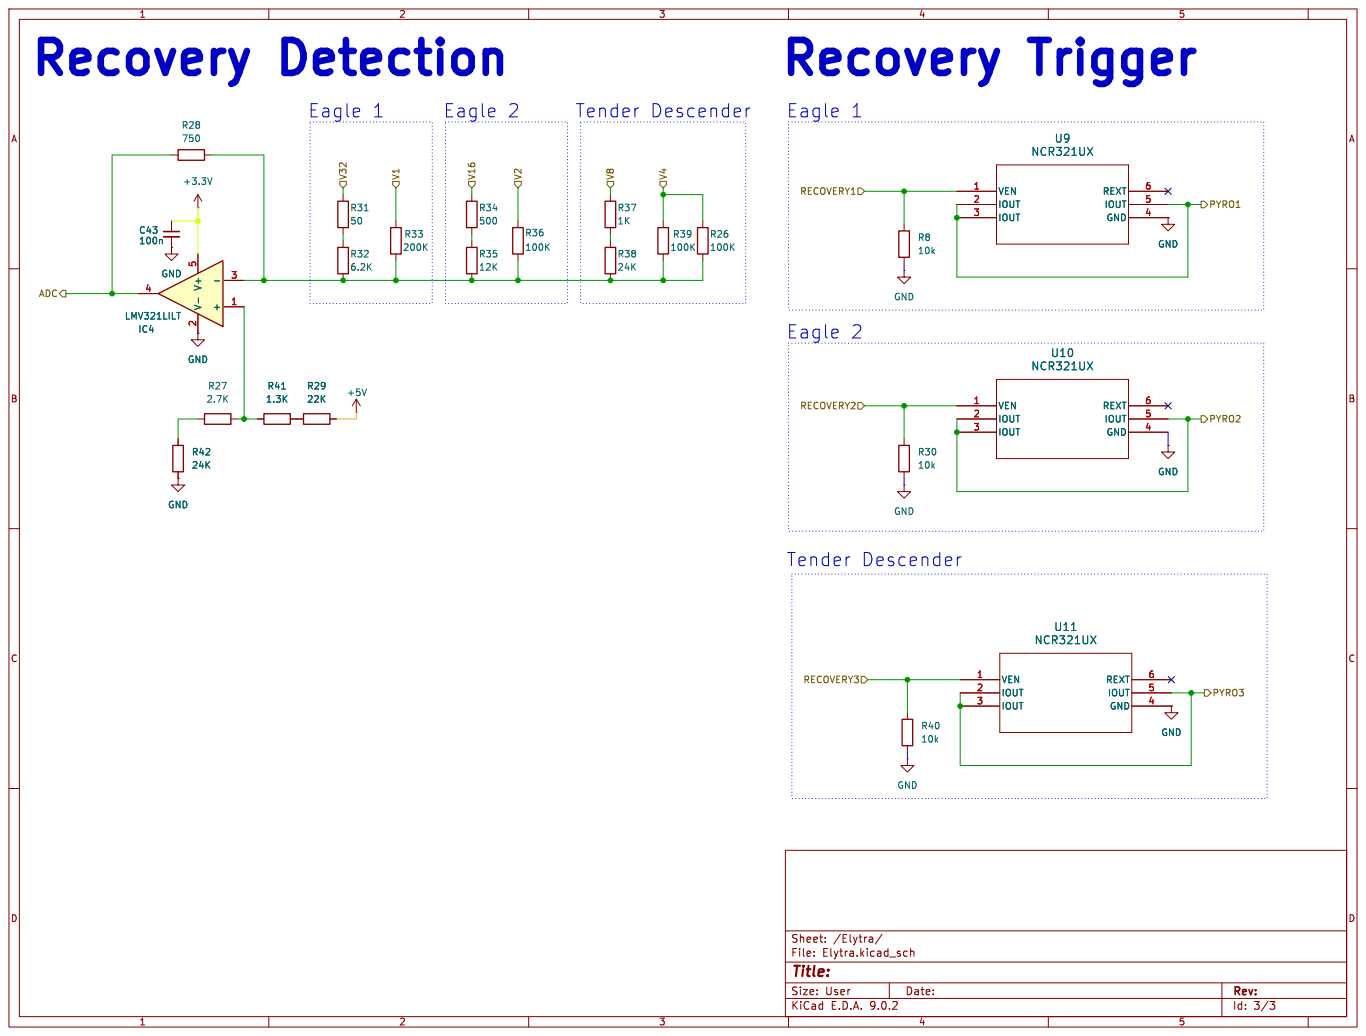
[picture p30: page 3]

Id: 3/3 Title: File: Elytra.kicad_sch Sheet: /Elytra/

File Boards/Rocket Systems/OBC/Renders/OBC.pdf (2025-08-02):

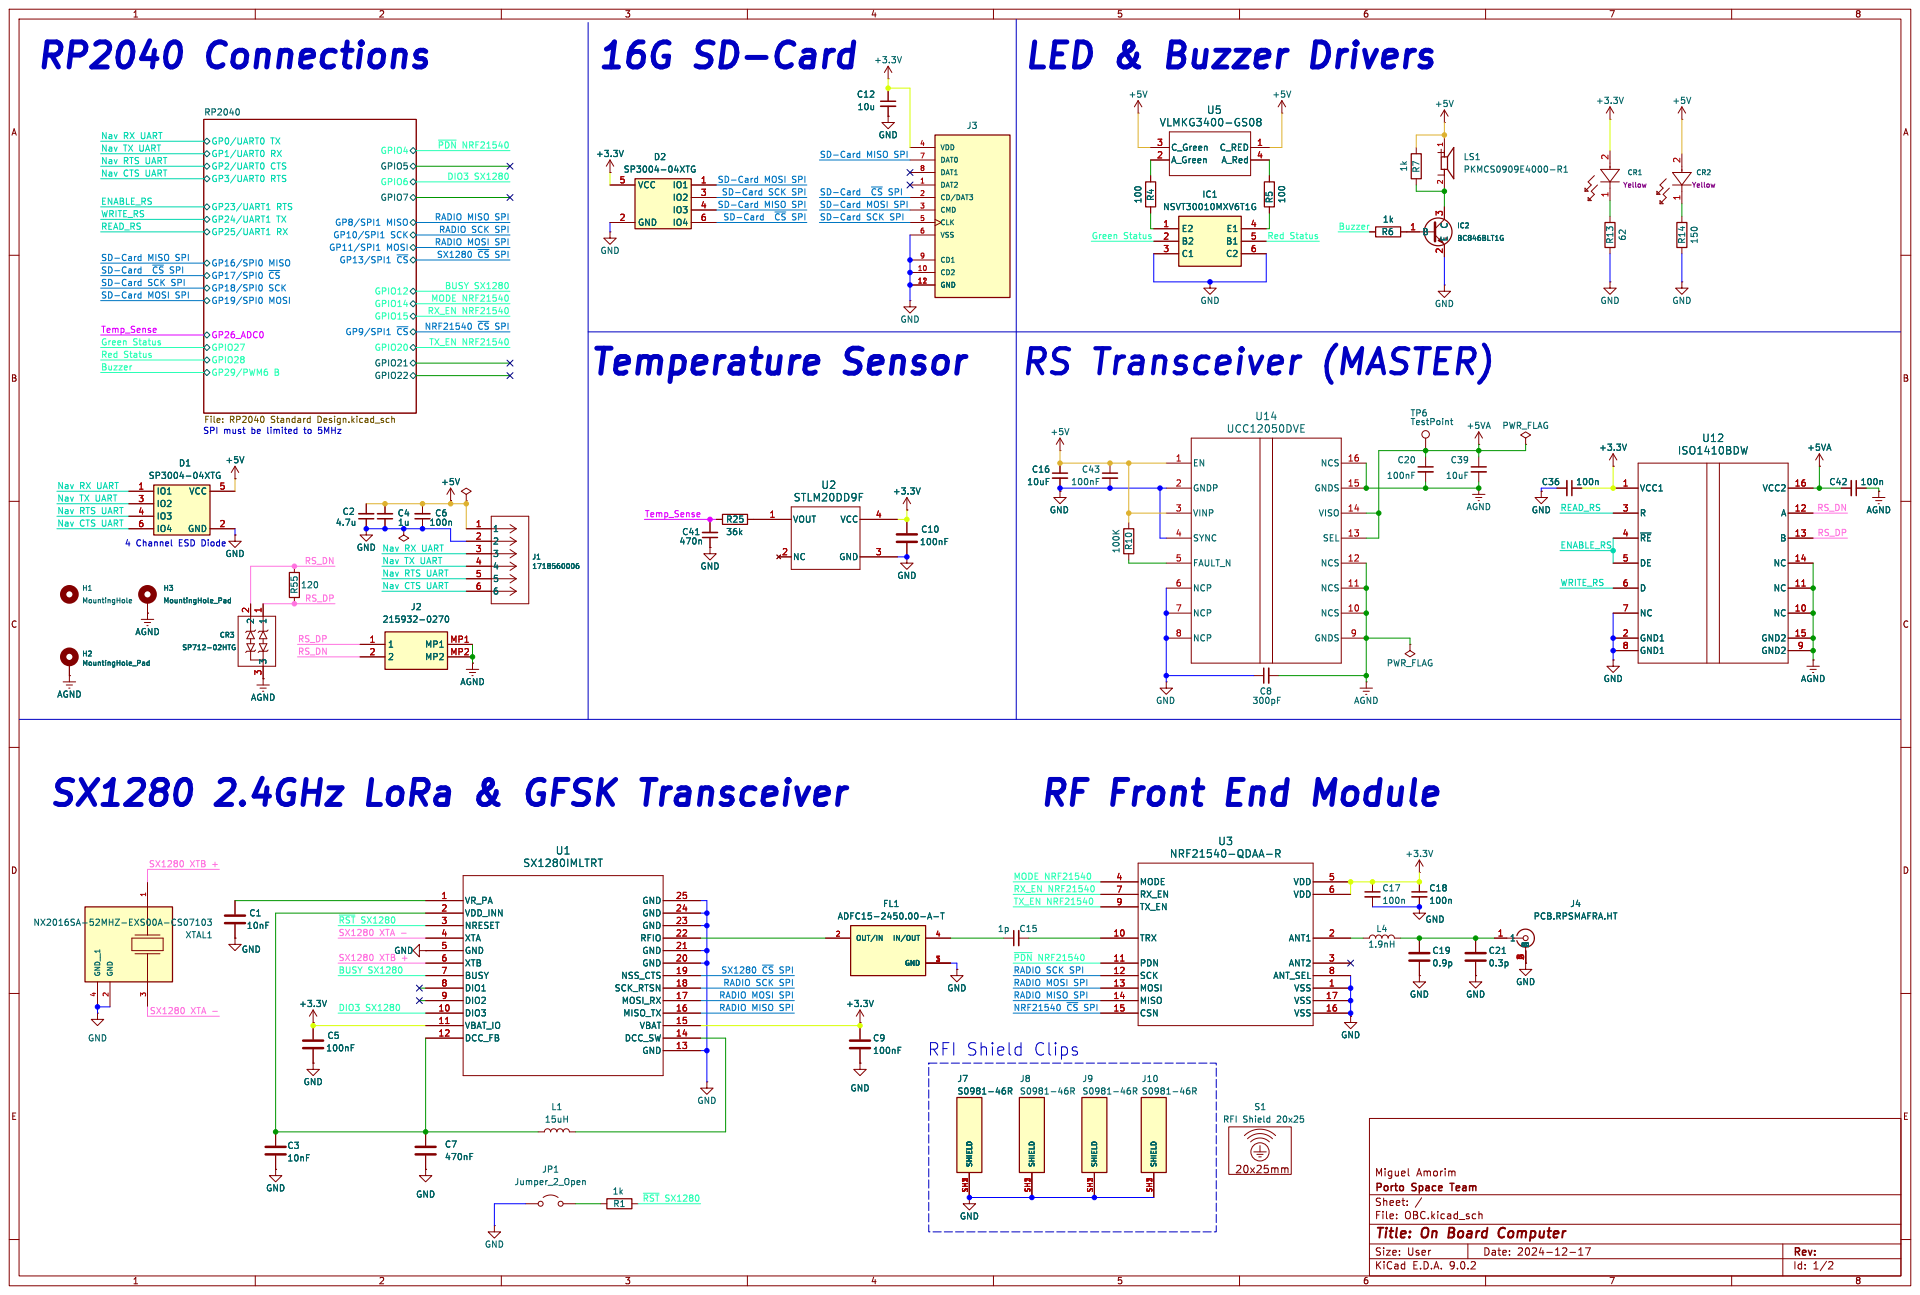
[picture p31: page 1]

1 2 LS1 PKMCS0909E4000-R1 H3 MountingHole_Pad MODE 4 RX_EN 7 TX_EN 9 TRX 10 PDN 11 SCK 12 MOSI 13 CSN 15 ANT1 2 ANT2 3 ANT_SEL 8 MISO 14 VDD 5 VDD 6 VSS 1 VSS 17 VSS 16 U3 NRF21540-QDAA-R

Temp_Sense SX1280 ~{CS}SPI RADIO SCK SPI NRF21540 ~{CS}SPI
RADIO MOSI SPI

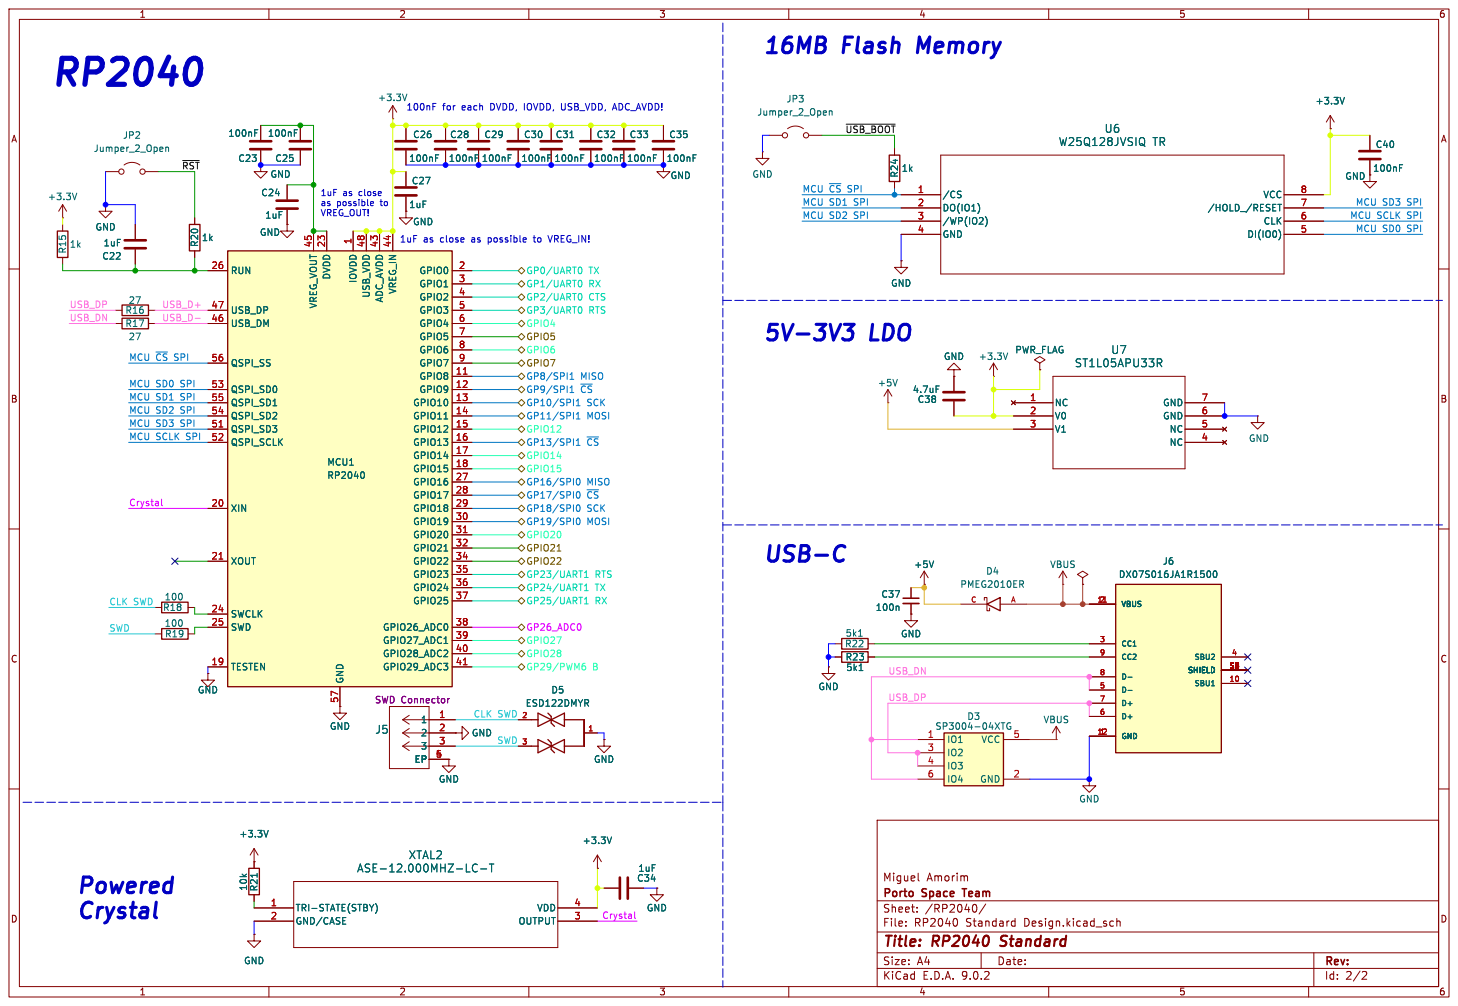
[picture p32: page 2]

100nF for each DVDD, IOVDD, USB_VDD, ADC_AVDD! 1uF as close

1 USB_VDD 48 ADC_AVDD 43 VREG_IN 44 GPIO0 2 GPIO1 3 GPIO2 4 GPIO3 5 GPIO4 6 GPIO5 7 GPIO6 8 GPIO7 9 GPIO8 11 GPIO9 12 GPIO10 13 GPIO11 14 GPIO12 15 GPIO13 16 GPIO14 17 GPIO15 18 GPIO16 27 GPIO17 28 GPIO18 29 GPIO19 30 GPIO20 31 GPIO21 32 GPIO22 34 GPIO23 35 GPIO24 36 GPIO25 37 GPIO26_ADC0 38 GPIO27_ADC1 39 GPIO28_ADC2 40 GPIO29_ADC3 41 MCU1 RP2040 R241k NC 1 V0 2 V1 3 GND 7 GND 6 NC 5 NC 4 U7 ST1L05APU33R

MCU SD3 SPI MCU SCLK SPI MCU SD0 SPI Crystal MCU SCLK SPI USB_D+ USB_DN

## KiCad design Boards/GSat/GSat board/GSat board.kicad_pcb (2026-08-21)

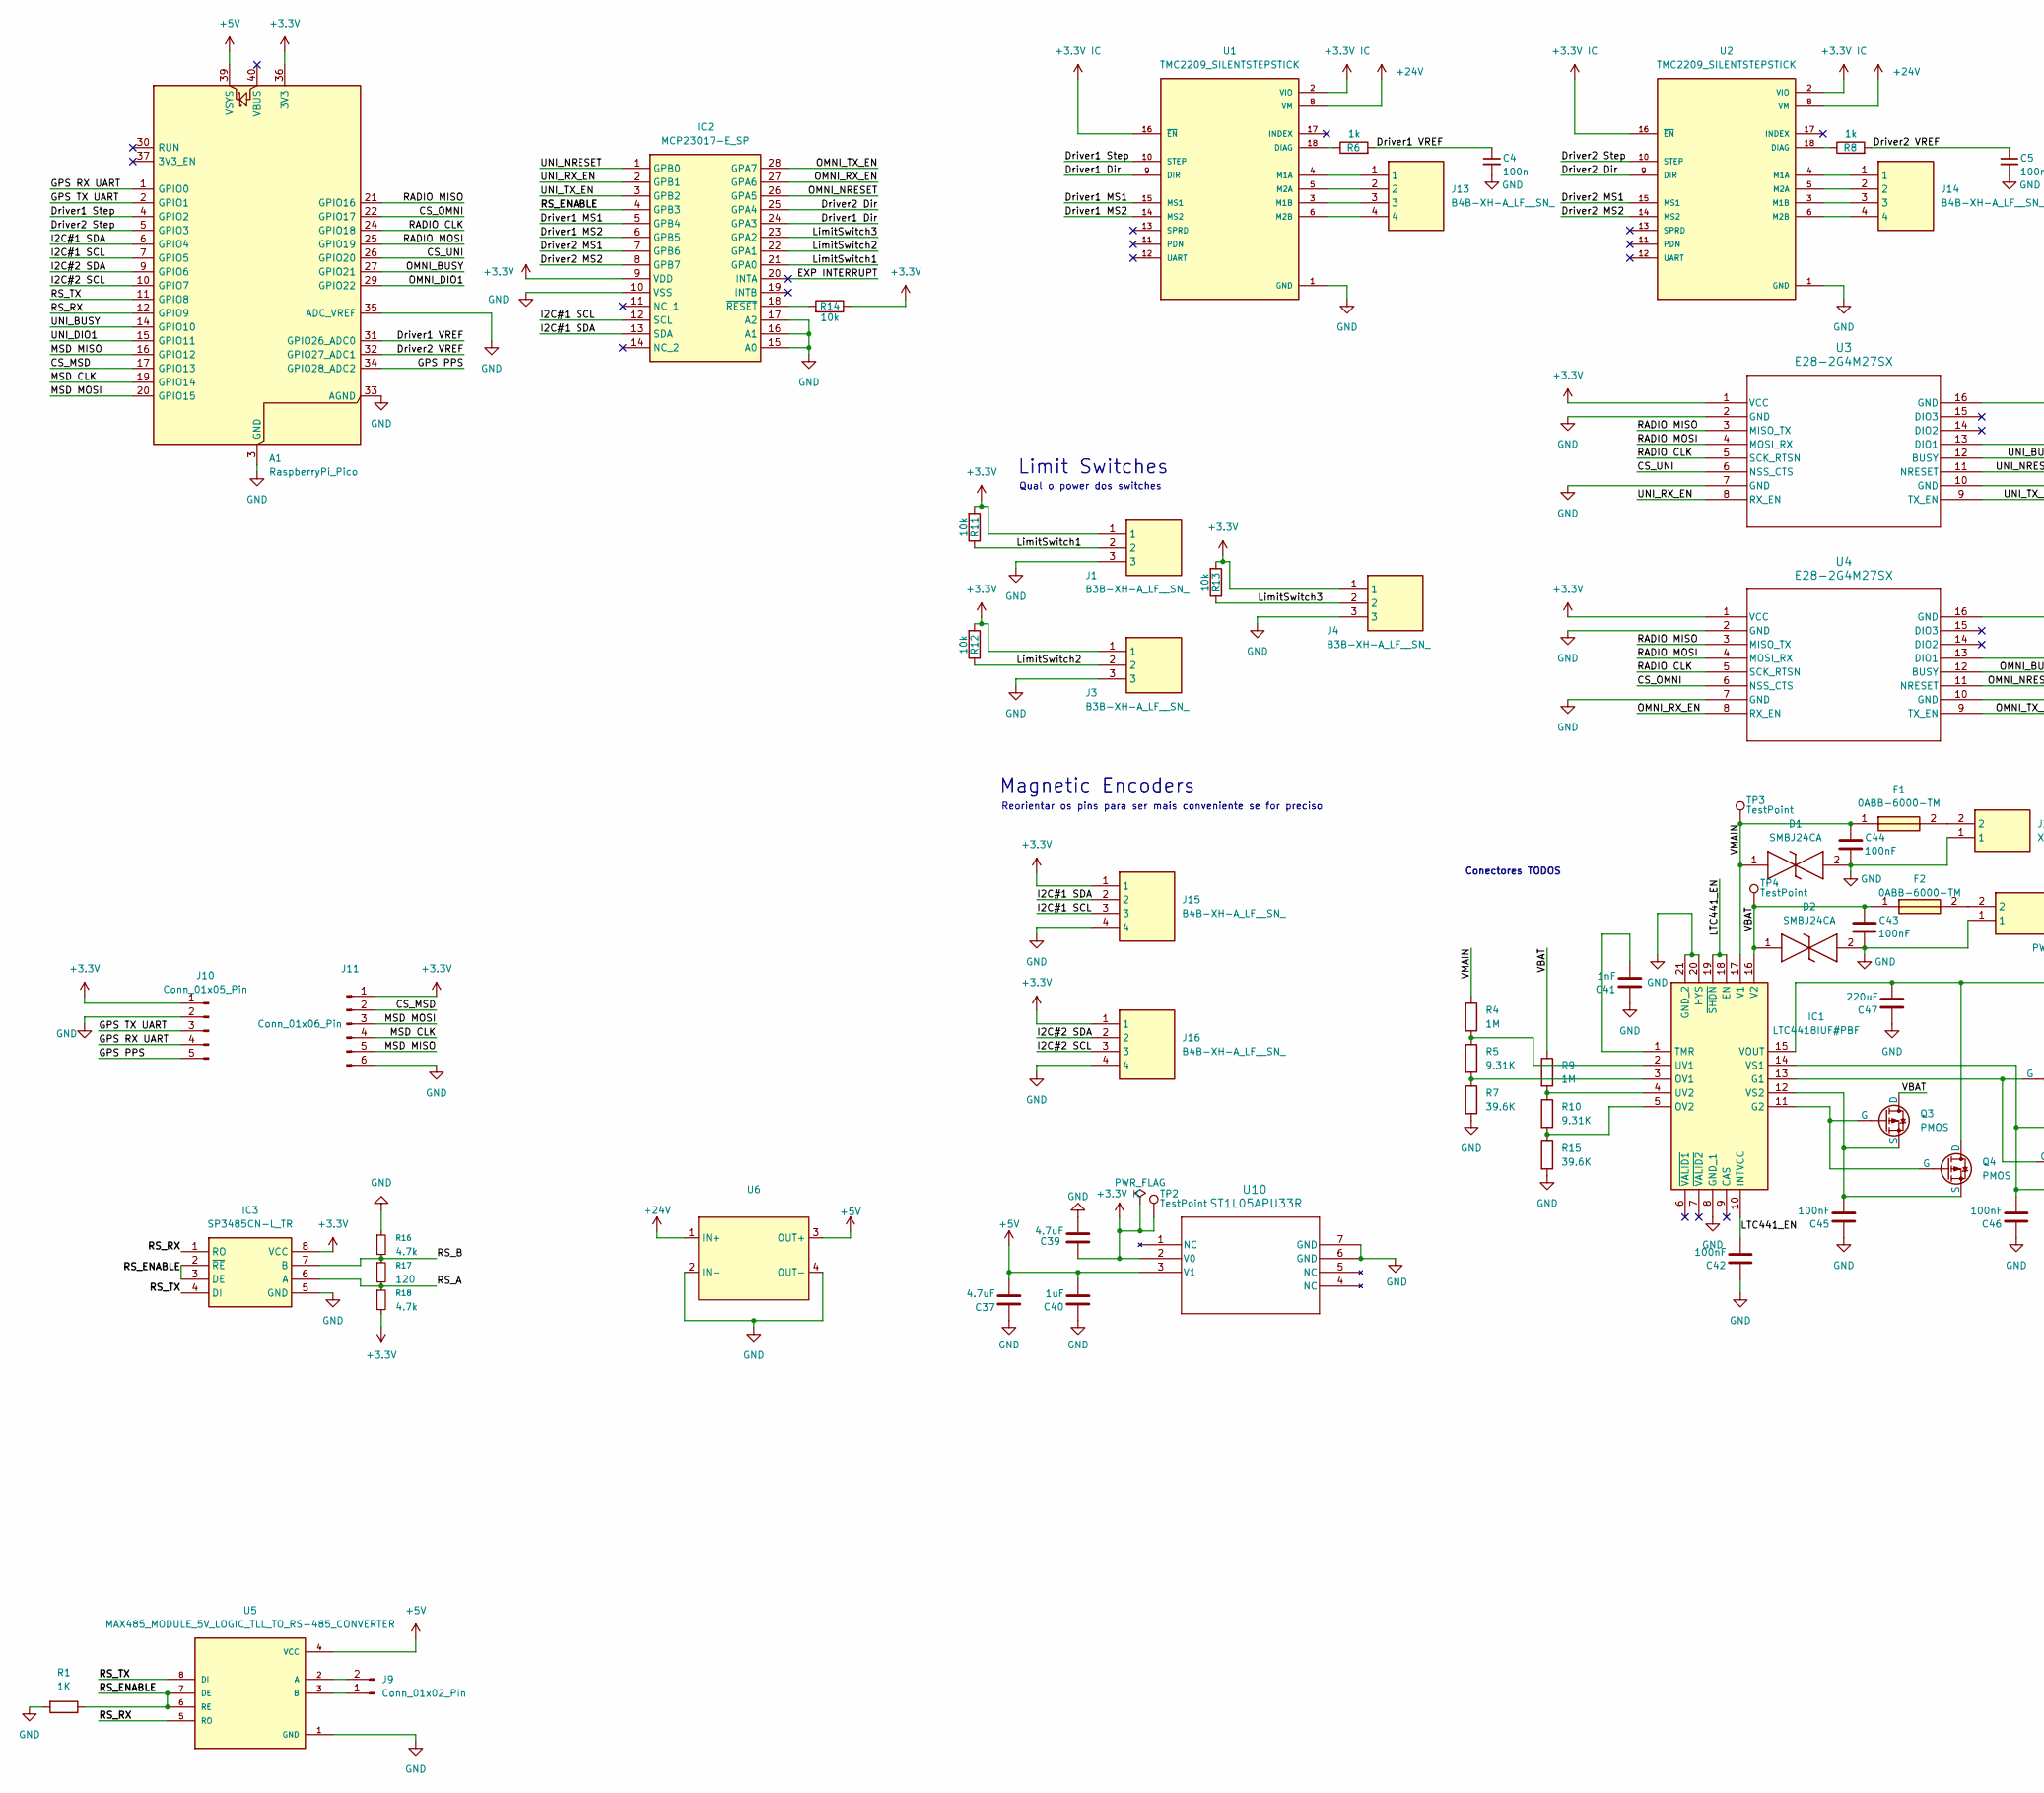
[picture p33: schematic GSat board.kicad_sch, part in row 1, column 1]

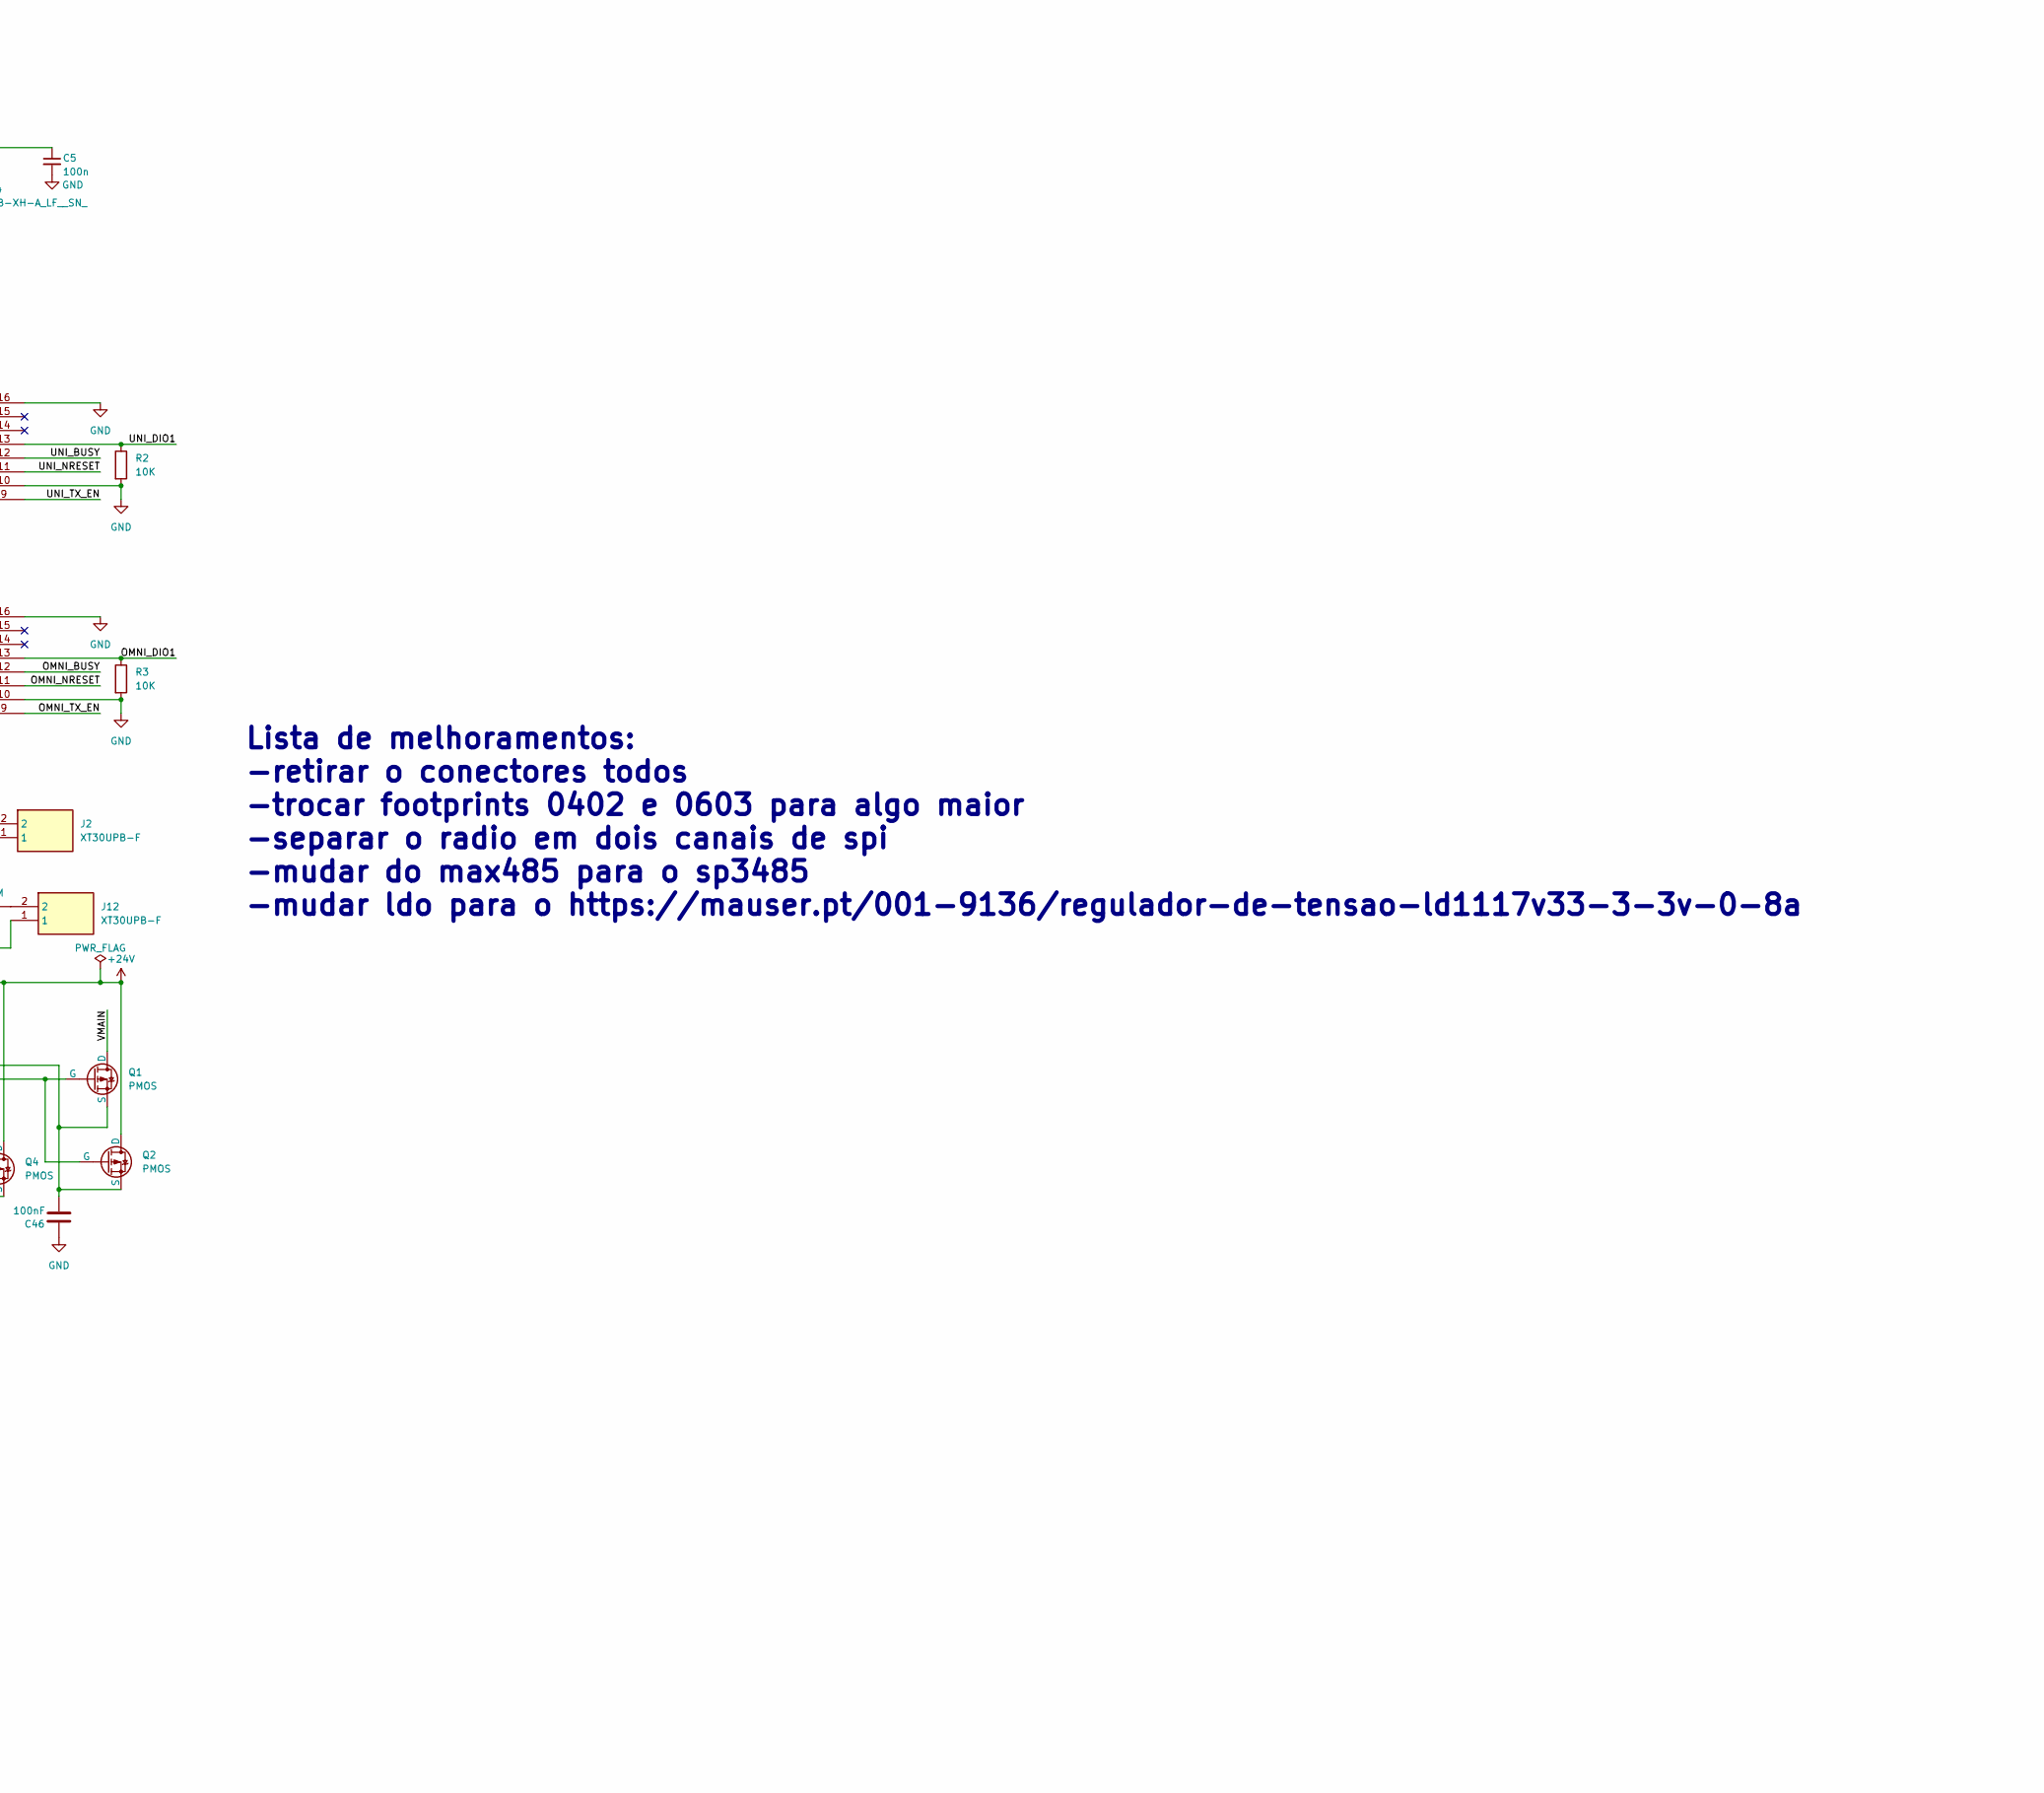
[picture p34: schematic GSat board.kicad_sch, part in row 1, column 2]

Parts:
A1: RaspberryPi_Pico; RaspberryPi_Pico_Common_Unspecified
C4, C5: 100n; Capacitor_0402
C37, C39: 4.7uF; Capacitor_0402
C40: 1uF; Capacitor_0402
C41: 1nF; Capacitor_0402
C42, C43, C44, C45, C46: 100nF; Capacitor_0402
C47: 220uF; Capacitor_0402
D1, D2: SMBJ24CA; DIOM5436X244N; Mouser Part Number 576-SMBJ24CA
F1, F2: 0ABB-6000-TM; 0ABB6000TM; Mouser Part Number 530-0ABB-6000-TM
IC1: LTC4418IUF#PBF; QFN50P400X400X80-21N-D; Mouser Part Number 584-LTC4418IUFPBF
IC2: MCP23017-E_SP; DIP794W56P254L3486H508Q28N; Mouser Part Number 579-MCP23017-E/SP
IC3: SP3485CN-L_TR; SOIC127P600X175-8N; Mouser Part Number 701-SP3485CN-L/TR
J1, J3, J4: B3B-XH-A_LF__SN_; B3BXHALFSN; Mouser Part Number 306-B3BXHALFSNP
J2, J12: XT30UPB-F; XT30UPBF; Manufacturer_Part_Number XT30UPB-F
J9: Conn_01x02_Pin
J10: Conn_01x05_Pin; PinSocket_1x05_P2.54mm_Vertical
J11: Conn_01x06_Pin; PinSocket_1x06_P2.54mm_Vertical
J13, J14, J15, J16: B4B-XH-A_LF__SN_; B4BXHALFSN; Mouser Part Number 306-B4BXHALFSN
Q1, Q2, Q3, Q4: PMOS; TO-252-3_TabPin2
R1: 1K; R_0603_1608Metric_Pad0.98x0.95mm_HandSolder
R2, R3: 10K; R_0603_1608Metric_Pad0.98x0.95mm_HandSolder
R4, R9: 1M; R_0603_1608Metric_Pad0.98x0.95mm_HandSolder
R5, R10: 9.31K; R_0603_1608Metric_Pad0.98x0.95mm_HandSolder
R6, R8: 1k; RES_0402
R7, R15: 39.6K; R_0603_1608Metric_Pad0.98x0.95mm_HandSolder
R11, R12, R13, R14: 10k; RES_0402
R16, R18: 4.7k; R_0603_1608Metric_Pad0.98x0.95mm_HandSolder
R17: 120; R_0603_1608Metric_Pad0.98x0.95mm_HandSolder
TP2, TP3, TP4: TestPoint; TestPoint_Pad_2.0x2.0mm
U1, U2: TMC2209_SILENTSTEPSTICK; MODULE_TMC2209_SILENTSTEPSTICK; PARTREV 1.20
U3, U4: E28-2G4M27SX; Radio_Module_PST
U5: MAX485_MODULE_5V_LOGIC_TLL_TO_RS-485_CONVERTER; MODULE_MAX485_MODULE_5V_LOGIC_TLL_TO_RS-485_CONVERTER; PARTREV 1r0
U6: DCDC_Module
U10: ST1L05APU33R; DFN_5APU33R_STM

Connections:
+3.3V: A1.36 (3V3), IC2.9 (VDD), IC3.8 (VCC), J1.1, J3.1, J4.1, J10.1, J11.1, J15.1, J16.1, R11.2, R12.2, R13.2, R14.1, R18.2, U3.1 (VCC), U4.1 (VCC)
+3.3V IC: C39.2, TP2.1 (1_1), U1.2 (VIO), U1.16 (~EN), U2.2 (VIO), U2.16 (~EN), U10.2 (V0)
+5V: A1.39 (VSYS), C37.2, C40.2, U5.4 (VCC), U6.3 (OUT+), U10.3 (V1)
+24V: C47.2, IC1.15 (VOUT), Q2.2 (D), Q4.2 (D), U1.8 (VM), U2.8 (VM), U6.1 (IN+)
/CS_MSD: A1.17 (GPIO13), J11.2
/CS_OMNI: A1.22 (GPIO17), U4.6 (NSS_CTS)
/CS_UNI: A1.26 (GPIO20), U3.6 (NSS_CTS)
/Driver1 Dir: IC2.24 (GPA3), U1.9 (DIR)
/Driver1 MS1: IC2.5 (GPB4), U1.15 (MS1)
/Driver1 MS2: IC2.6 (GPB5), U1.14 (MS2)
/Driver1 Step: A1.4 (GPIO2), U1.10 (STEP)
/Driver1 VREF: A1.31 (GPIO26_ADC0), C4.1, R6.2
/Driver2 Dir: IC2.25 (GPA4), U2.9 (DIR)
/Driver2 MS1: IC2.7 (GPB6), U2.15 (MS1)
/Driver2 MS2: IC2.8 (GPB7), U2.14 (MS2)
/Driver2 Step: A1.5 (GPIO3), U2.10 (STEP)
/Driver2 VREF: A1.32 (GPIO27_ADC1), C5.1, R8.2
/EXP INTERRUPT: IC2.20 (INTA)
/GPS PPS: A1.34 (GPIO28_ADC2), J10.5
/GPS RX UART: A1.1 (GPIO0), J10.4
/GPS TX UART: A1.2 (GPIO1), J10.3
/I2C#1 SCL: A1.7 (GPIO5), IC2.12 (SCL), J15.3
/I2C#1 SDA: A1.6 (GPIO4), IC2.13 (SDA), J15.2
/I2C#2 SCL: A1.10 (GPIO7), J16.3
/I2C#2 SDA: A1.9 (GPIO6), J16.2
/LTC441_EN: C42.2, IC1.10 (INTVCC), IC1.18 (EN), IC1.19 (~SHDN)
/LimitSwitch1: IC2.21 (GPA0), J1.2, R11.1
/LimitSwitch2: IC2.22 (GPA1), J3.2, R12.1
/LimitSwitch3: IC2.23 (GPA2), J4.2, R13.1
/MSD CLK: A1.19 (GPIO14), J11.4
/MSD MISO: A1.16 (GPIO12), J11.5
/MSD MOSI: A1.20 (GPIO15), J11.3
/OMNI_BUSY: A1.27 (GPIO21), U4.12 (BUSY)
/OMNI_DIO1: A1.29 (GPIO22), R3.1, U4.13 (DIO1)
/OMNI_NRESET: IC2.26 (GPA5), U4.11 (NRESET)
/OMNI_RX_EN: IC2.27 (GPA6), U4.8 (RX_EN)
/OMNI_TX_EN: IC2.28 (GPA7), U4.9 (TX_EN)
/RADIO CLK: A1.24 (GPIO18), U3.5 (SCK_RTSN), U4.5 (SCK_RTSN)
/RADIO MISO: A1.21 (GPIO16), U3.3 (MISO_TX), U4.3 (MISO_TX)
/RADIO MOSI: A1.25 (GPIO19), U3.4 (MOSI_RX), U4.4 (MOSI_RX)
/RS_A: IC3.6 (A), R17.2, R18.1
/RS_B: IC3.7 (B), R16.2, R17.1
/RS_ENABLE: IC2.4 (GPB3), IC3.2 (~RE), IC3.3 (DE), R1.1, U5.6 (RE), U5.7 (DE)
/RS_RX: A1.12 (GPIO9), IC3.1 (RO), U5.5 (RO)
/RS_TX: A1.11 (GPIO8), IC3.4 (DI), U5.8 (DI)
/UNI_BUSY: A1.14 (GPIO10), U3.12 (BUSY)
/UNI_DIO1: A1.15 (GPIO11), R2.1, U3.13 (DIO1)
/UNI_NRESET: IC2.1 (GPB0), U3.11 (NRESET)
/UNI_RX_EN: IC2.2 (GPB1), U3.8 (RX_EN)
/UNI_TX_EN: IC2.3 (GPB2), U3.9 (TX_EN)
/VBAT: C43.1, D2.1, F2.1, IC1.16 (V2), Q3.2 (D), R9.1, TP4.1 (1_1)
/VMAIN: C44.1, D1.1, F1.1, IC1.17 (V1), Q1.2 (D), R4.1, TP3.1 (1_1)
GND: A1.3 (GND), A1.8 (GND), A1.13 (GND), A1.18 (GND), A1.23 (GND), A1.28 (GND), A1.33 (AGND), A1.35 (ADC_VREF), A1.38 (GND), C4.2, C5.2, C37.1, C39.1, C40.1, C41.1, C42.1, C43.2, C44.2, C45.1, C46.1, C47.1, D1.2, D2.2, IC1.8 (GND_1), IC1.20 (HYS), IC1.21 (GND_2), IC2.10 (VSS), IC2.15 (A0), IC2.16 (A1), IC2.17 (A2), IC3.5 (GND), J1.3, J2.1, J3.3, J4.3, J10.2, J11.6, J12.1, J15.4, J16.4, R1.2, R2.2, R3.2, R7.2, R15.2, R16.1, U1.1 (GND), U1.7 (GND), U2.1 (GND), U2.7 (GND), U3.2 (GND), U3.7 (GND), U3.10 (GND), U3.16 (GND), U4.2 (GND), U4.7 (GND), U4.10 (GND), U4.16 (GND), U5.1 (GND), U6.2 (IN-), U6.4 (OUT-), U10.6 (GND), U10.7 (GND)
unnamed: F1.2, J2.2
unnamed: F2.2, J12.2
unnamed: IC1.13 (G1), Q1.1 (G), Q2.1 (G)
unnamed: IC1.11 (G2), Q3.1 (G), Q4.1 (G)
unnamed: IC1.3 (OV1), R5.2, R7.1
unnamed: IC1.5 (OV2), R10.2, R15.1
unnamed: C41.2, IC1.1 (TMR)
unnamed: IC1.2 (UV1), R4.2, R5.1
unnamed: IC1.4 (UV2), R9.2, R10.1
unnamed: C46.2, IC1.14 (VS1), Q1.3 (S), Q2.3 (S)
unnamed: C45.2, IC1.12 (VS2), Q3.3 (S), Q4.3 (S)
unnamed: IC2.18 (~RESET), R14.2
unnamed: J9.1, U5.3 (B)
unnamed: J9.2, U5.2 (A)
unnamed: R6.1, U1.18 (DIAG)
unnamed: J13.1, U1.4 (M1A)
unnamed: J13.3, U1.3 (M1B)
unnamed: J13.2, U1.5 (M2A)
unnamed: J13.4, U1.6 (M2B)
unnamed: R8.1, U2.18 (DIAG)
unnamed: J14.1, U2.4 (M1A)
unnamed: J14.3, U2.3 (M1B)
unnamed: J14.2, U2.5 (M2A)
unnamed: J14.4, U2.6 (M2B)

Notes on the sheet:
Lista de melhoramentos: -retirar o conectores todos -trocar footprints 0402 e 0603 para algo maior -separar o radio em dois canais de spi -mudar do max485 para o sp3485 -mudar ldo para o https://mauser.pt/001-9136/regulador-de-tensao-ld1117v33-3-3v-0-8a
Reorientar os pins para ser mais conveniente se for preciso
Conectores TODOS
Qual o power dos switches
Magnetic Encoders
Limit Switches

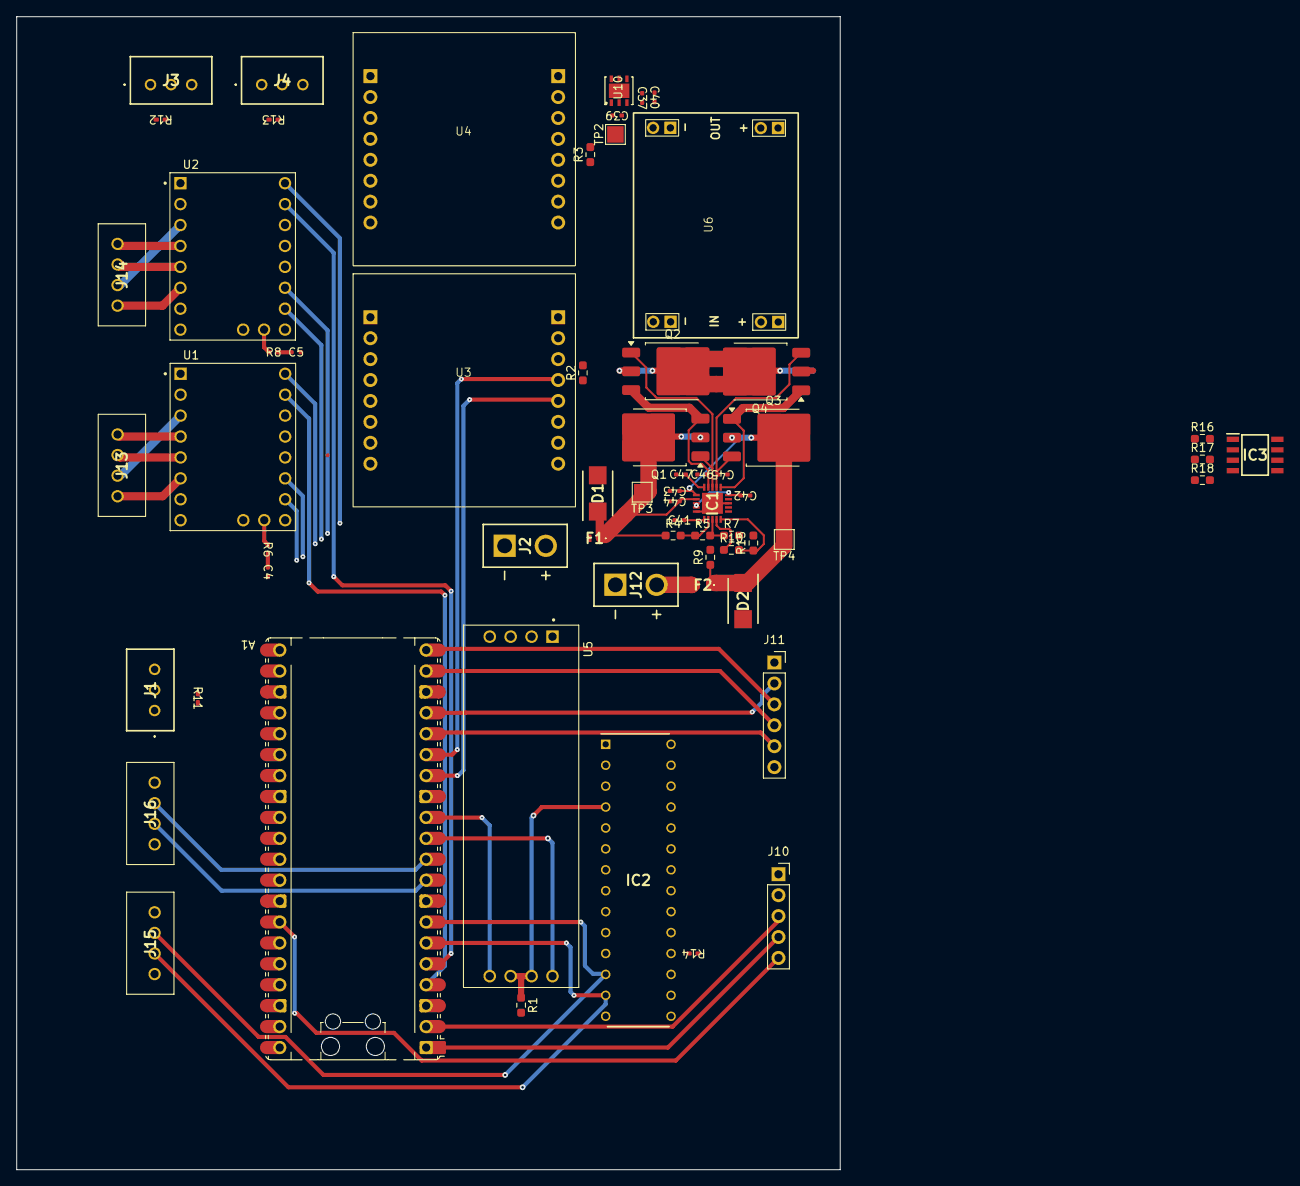
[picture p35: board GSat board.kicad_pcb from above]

Board: 2 copper layers, 100.0 x 140.0 mm, 63 parts (0 on the bottom side), 74 nets.

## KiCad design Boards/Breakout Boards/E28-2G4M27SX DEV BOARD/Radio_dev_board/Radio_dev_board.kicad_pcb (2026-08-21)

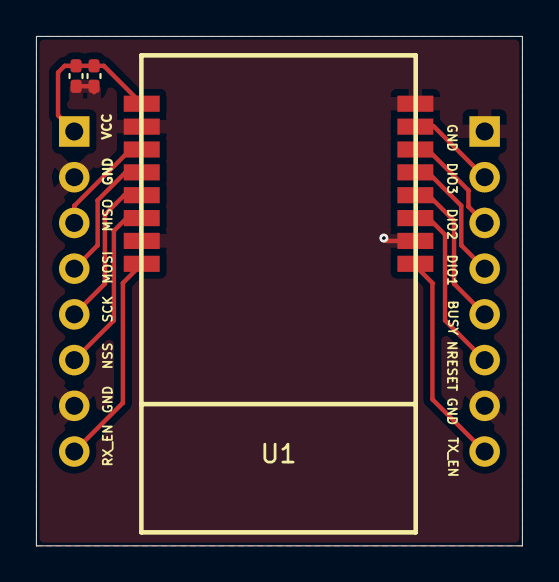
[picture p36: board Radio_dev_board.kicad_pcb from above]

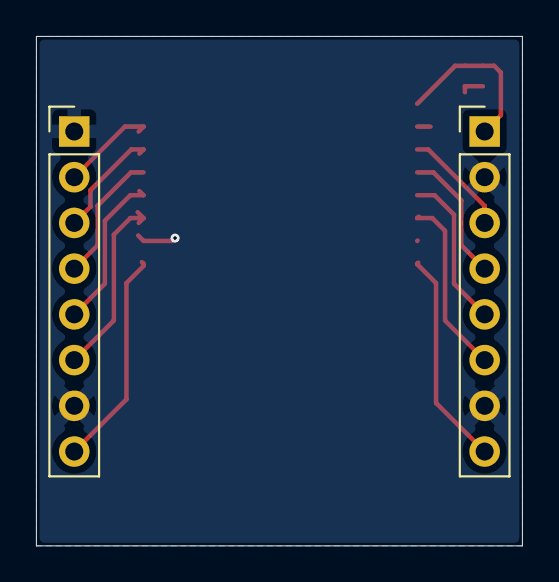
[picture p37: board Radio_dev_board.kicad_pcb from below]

Board: 2 copper layers, 27.0 x 28.3 mm, 5 parts (2 on the bottom side), 13 nets.

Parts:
C1: 0.1uF; C_0402_1005Metric_Pad0.74x0.62mm_HandSolder
C2: 100uF; C_0402_1005Metric_Pad0.74x0.62mm_HandSolder
J1, J2: Conn_01x08_Pin; PinHeader_1x08_P2.54mm_Vertical
U1: E28-2G4M27SX; E28-2G4M27S

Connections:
GND: C1.2, C2.2, J1.2, J1.7, J2.10 (Pin_7), J2.16 (Pin_1), U1.2 (GND), U1.7 (GND), U1.10 (GND), U1.16 (GND)
unnamed: J1.3, U1.3 (MISO_TX)
unnamed: J1.4, U1.4 (MOSI_RX)
unnamed: J1.5, U1.5 (SCK_RTSN)
unnamed: J1.6, U1.6 (NSS_CTS)
unnamed: J1.8, U1.8 (RX_EN)
unnamed: J2.15 (Pin_2), U1.15 (DIO3)
unnamed: J2.14 (Pin_3), U1.14 (DIO2)
unnamed: J2.13 (Pin_4), U1.13 (DIO1)
unnamed: J2.12 (Pin_5), U1.12 (BUSY)
unnamed: J2.11 (Pin_6), U1.11 (NRESET)
unnamed: J2.9 (Pin_8), U1.9 (TX_EN)
VCC: C1.1, C2.1, J1.1, U1.1 (VCC)

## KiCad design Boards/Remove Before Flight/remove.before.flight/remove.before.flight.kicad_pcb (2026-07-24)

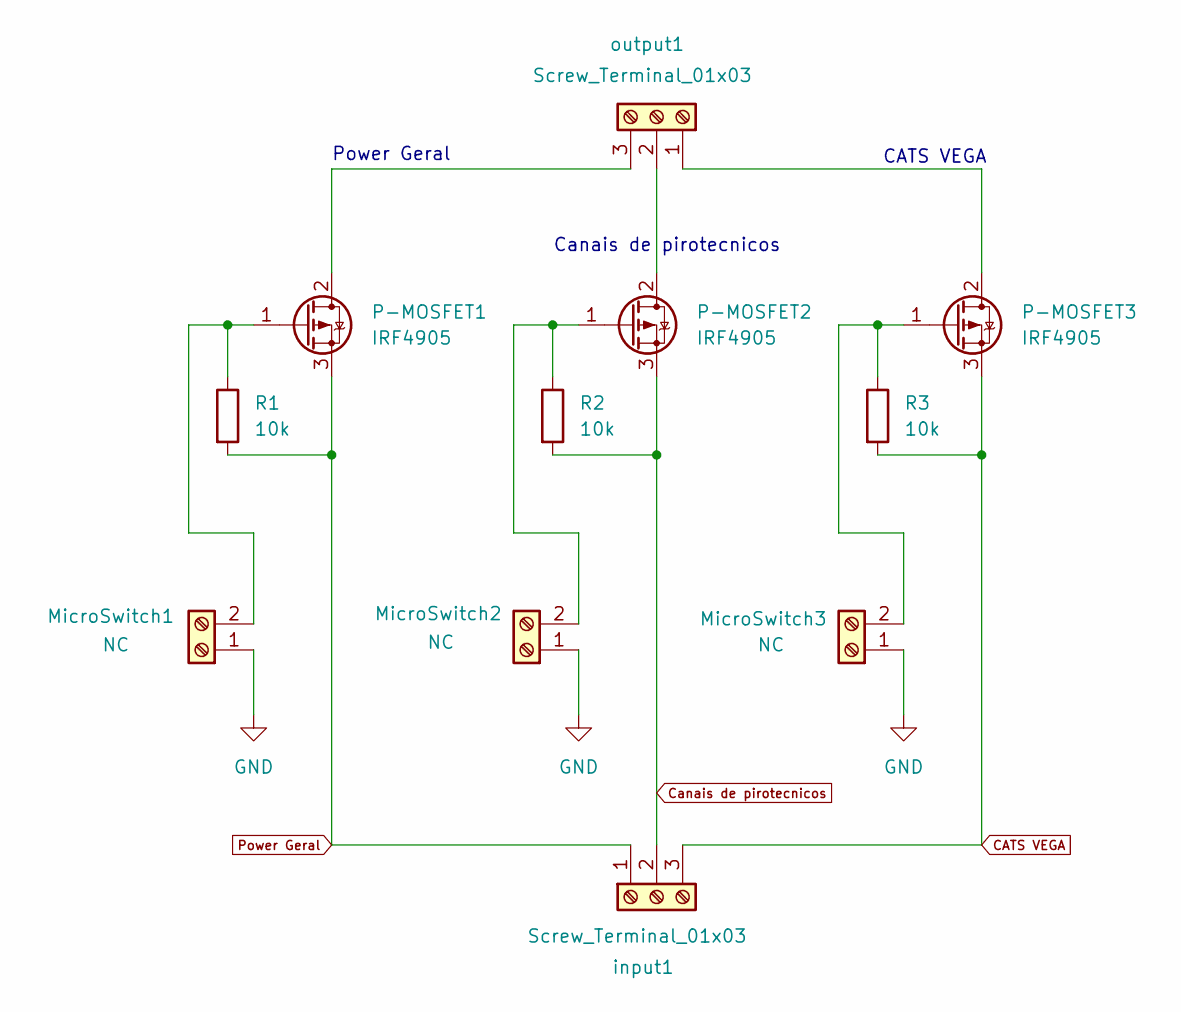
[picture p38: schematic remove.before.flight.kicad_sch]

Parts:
MicroSwitch1, MicroSwitch2, MicroSwitch3: NC; TerminalBlock_Xinya_XY308-2.54-2P_1x02_P2.54mm_Horizontal
P-MOSFET1, P-MOSFET2, P-MOSFET3: IRF4905; TO-220-3_Vertical
R1, R2, R3: 10k; R_Axial_DIN0207_L6.3mm_D2.5mm_P10.16mm_Horizontal
input1: Screw_Terminal_01x03; TerminalBlock_Xinya_XY308-2.54-3P_1x03_P2.54mm_Horizontal
output1: Screw_Terminal_01x03; TerminalBlock_Xinya_XY308-2.54-3P_1x03_P2.54mm_Horizontal

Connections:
CATS VEGA: P-MOSFET3.3 (S), R3.2, input1.3
Canais de pirotecnicos: P-MOSFET2.3 (S), R2.2, input1.2
GND: MicroSwitch1.1, MicroSwitch2.1, MicroSwitch3.1
unnamed: MicroSwitch1.2, P-MOSFET1.1 (G), R1.1
unnamed: MicroSwitch2.2, P-MOSFET2.1 (G), R2.1
unnamed: MicroSwitch3.2, P-MOSFET3.1 (G), R3.1
unnamed: P-MOSFET1.2 (D), output1.3
unnamed: P-MOSFET2.2 (D), output1.2
unnamed: P-MOSFET3.2 (D), output1.1
Power Geral: P-MOSFET1.3 (S), R1.2, input1.1

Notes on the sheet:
CATS VEGA
Power Geral
Canais de pirotecnicos

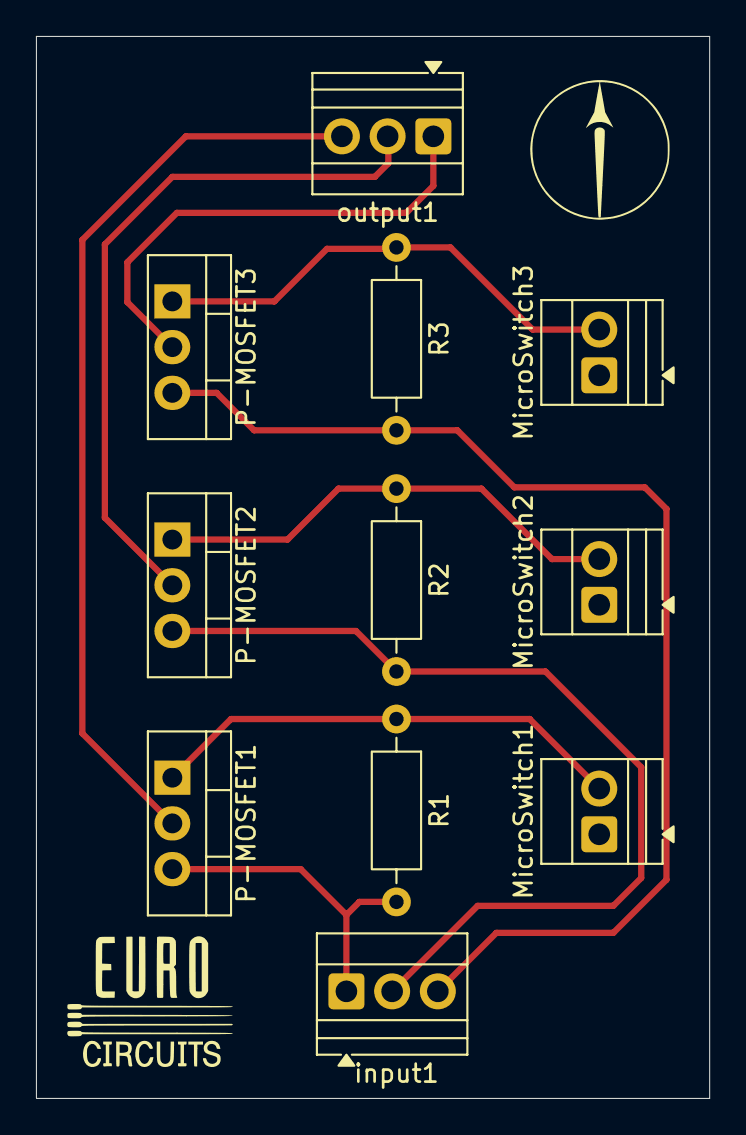
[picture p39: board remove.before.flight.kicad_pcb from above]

Board: 2 copper layers, 37.4 x 59.0 mm, 11 parts (0 on the bottom side), 10 nets.

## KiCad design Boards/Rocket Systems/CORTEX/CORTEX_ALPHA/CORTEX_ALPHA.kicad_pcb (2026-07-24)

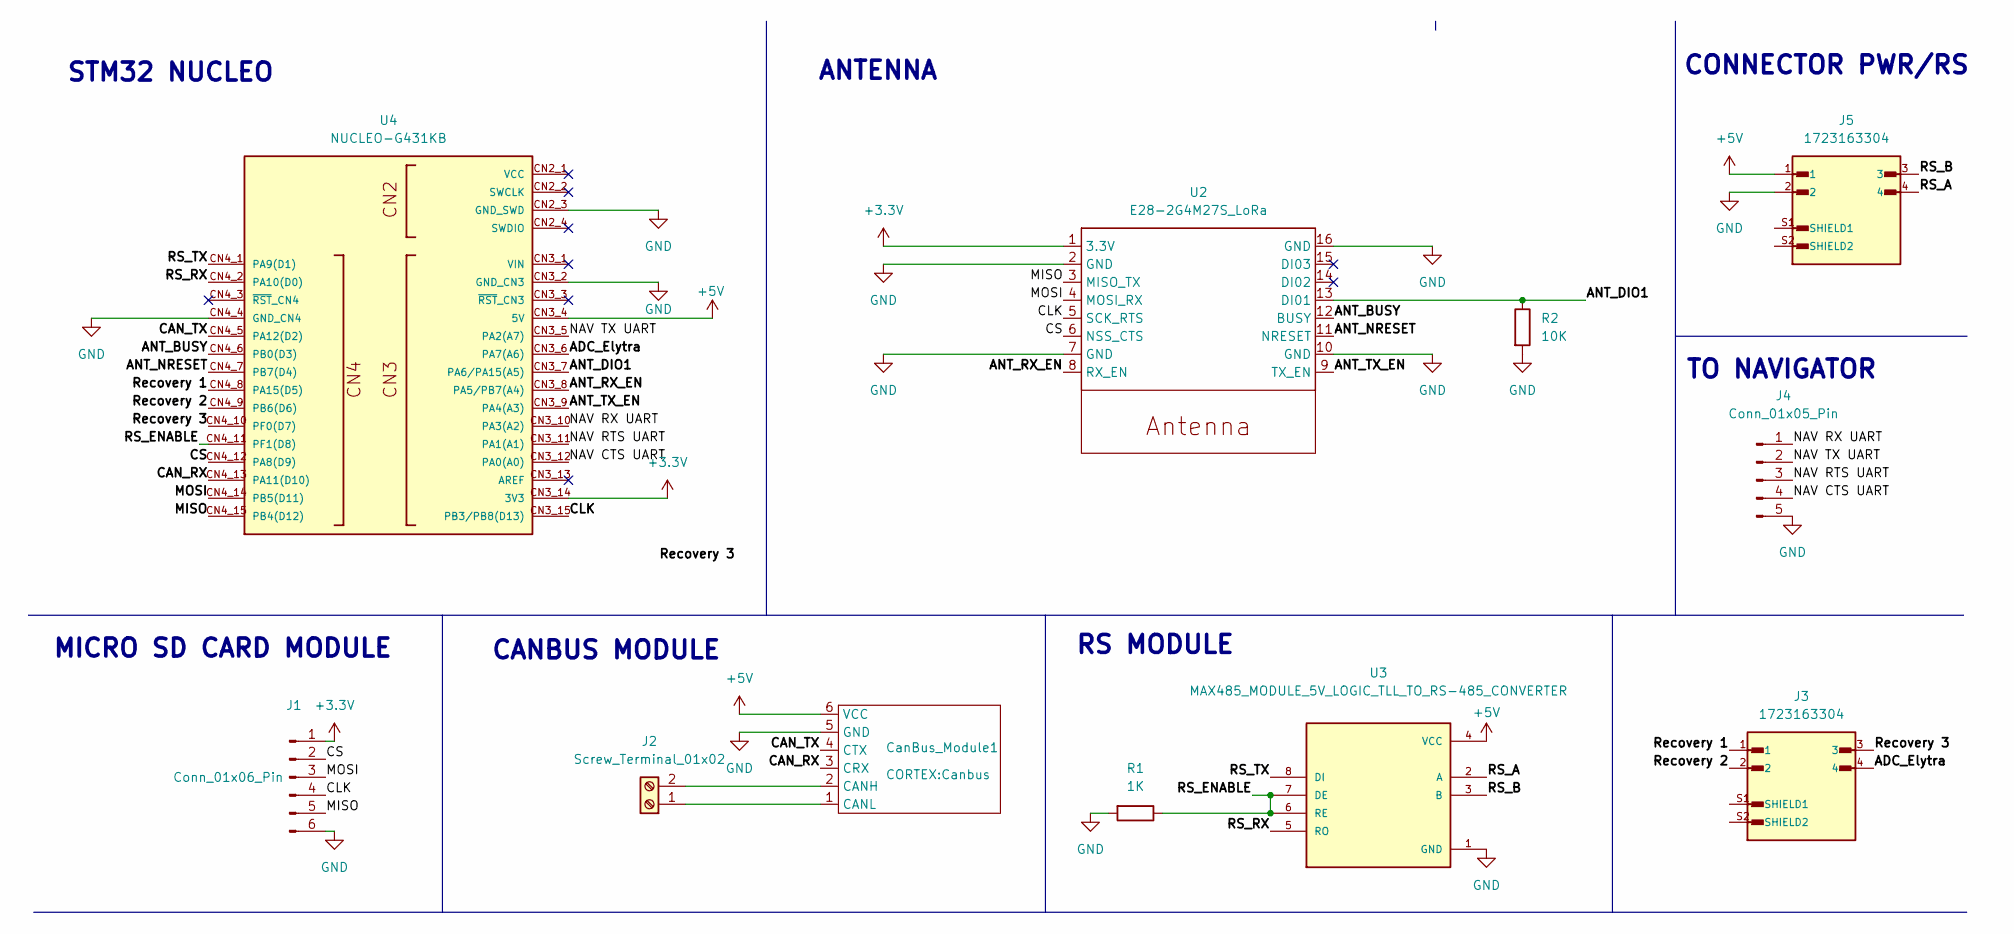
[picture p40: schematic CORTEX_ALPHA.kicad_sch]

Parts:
CanBus_Module1: Canbus
J1: Conn_01x06_Pin; PinSocket_1x06_P2.54mm_Vertical
J2: Screw_Terminal_01x02; TerminalBlock_Xinya_XY308-2.54-2P_1x02_P2.54mm_Horizontal
J3, J5: 1723163304; MOLEX_1723163304; PARTREV D
J4: Conn_01x05_Pin; PinHeader_1x05_P2.54mm_Vertical
R1: 1K; R_0603_1608Metric_Pad0.98x0.95mm_HandSolder
R2: 10K; R_0603_1608Metric_Pad0.98x0.95mm_HandSolder
U2: E28-2G4M27S_LoRa; Radio_Module_PST
U3: MAX485_MODULE_5V_LOGIC_TLL_TO_RS-485_CONVERTER; MODULE_MAX485_MODULE_5V_LOGIC_TLL_TO_RS-485_CONVERTER; PARTREV 1r0
U4: NUCLEO-G431KB; MODULE_NUCLEO-G431KB; PARTREV 2

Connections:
+3.3V: J1.1, U2.1 (3.3V), U4.CN3_14 (3V3)
+5V: CanBus_Module1.6 (VCC), J5.1, U3.4 (VCC), U4.CN3_4 (5V)
/ADC_Elytra: J3.4, U4.CN3_6 (PA7(A6))
/ANT_BUSY: U2.12 (BUSY), U4.CN4_6 (PB0(D3))
/ANT_DIO1: R2.1, U2.13 (DI01), U4.CN3_7 (PA6/PA15(A5))
/ANT_NRESET: U2.11 (NRESET), U4.CN4_7 (PB7(D4))
/ANT_RX_EN: U2.8 (RX_EN), U4.CN3_8 (PA5/PB7(A4))
/ANT_TX_EN: U2.9 (TX_EN), U4.CN3_9 (PA4(A3))
/CAN_RX: CanBus_Module1.3 (CRX), U4.CN4_13 (PA11(D10))
/CAN_TX: CanBus_Module1.4 (CTX), U4.CN4_5 (PA12(D2))
/CLK: J1.4, U2.5 (SCK_RTS), U4.CN3_15 (PB3/PB8(D13))
/CS: J1.2, U2.6 (NSS_CTS), U4.CN4_12 (PA8(D9))
/MISO: J1.5, U2.3 (MISO_TX), U4.CN4_15 (PB4(D12))
/MOSI: J1.3, U2.4 (MOSI_RX), U4.CN4_14 (PB5(D11))
/NAV CTS UART: J4.4, U4.CN3_12 (PA0(A0))
/NAV RTS UART: J4.3, U4.CN3_11 (PA1(A1))
/NAV RX UART: J4.1, U4.CN3_10 (PA3(A2))
/NAV TX UART: J4.2, U4.CN3_5 (PA2(A7))
/RS_A: J5.4, U3.2 (A)
/RS_B: J5.3, U3.3 (B)
/RS_ENABLE: R1.1, U3.6 (RE), U3.7 (DE), U4.CN4_11 (PF1(D8))
/RS_RX: U3.5 (RO), U4.CN4_2 (PA10(D0))
/RS_TX: U3.8 (DI), U4.CN4_1 (PA9(D1))
/Recovery 1: J3.1, U4.CN4_8 (PA15(D5))
/Recovery 2: J3.2, U4.CN4_9 (PB6(D6))
/Recovery 3: J3.3, U4.CN4_10 (PF0(D7))
GND: CanBus_Module1.5 (GND), J1.6, J4.5, J5.2, R1.2, R2.2, U2.2 (GND), U2.7 (GND), U2.10 (GND), U2.16 (GND), U3.1 (GND), U4.CN2_3 (GND_SWD), U4.CN3_2 (GND_CN3), U4.CN4_4 (GND_CN4)
unnamed: CanBus_Module1.2 (CANH), J2.2
unnamed: CanBus_Module1.1 (CANL), J2.1

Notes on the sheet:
STM32 NUCLEO
TO NAVIGATOR
RS MODULE
CANBUS MODULE
CONNECTOR PWR/RS
MICRO SD CARD MODULE
ANTENNA

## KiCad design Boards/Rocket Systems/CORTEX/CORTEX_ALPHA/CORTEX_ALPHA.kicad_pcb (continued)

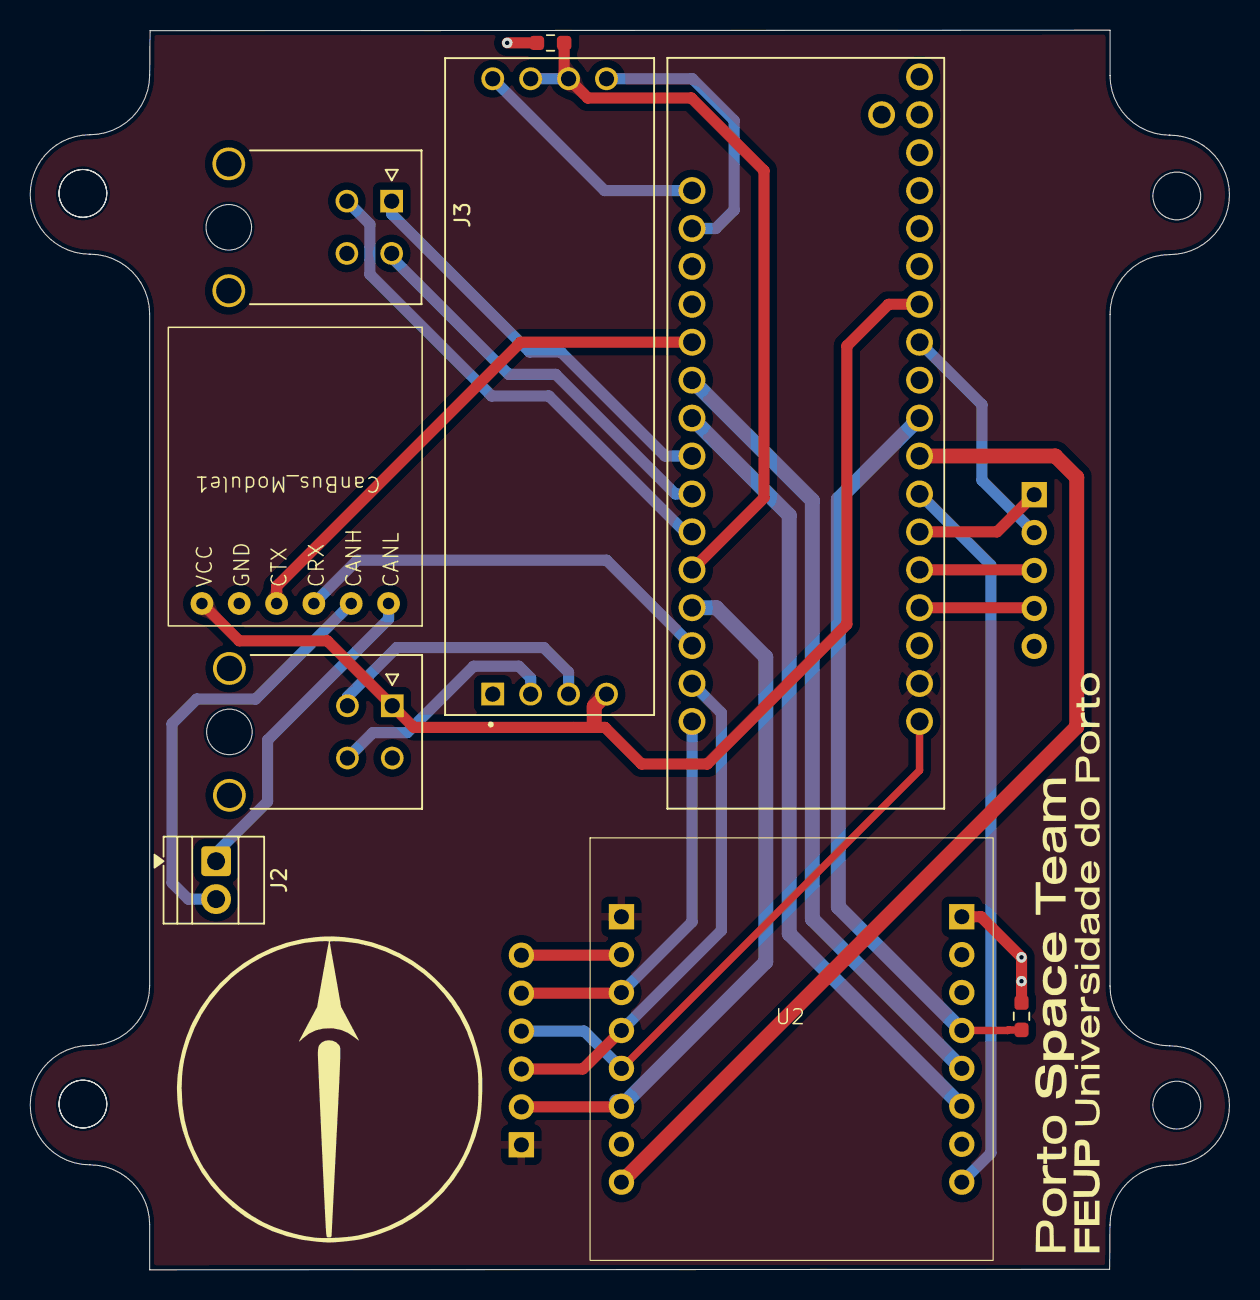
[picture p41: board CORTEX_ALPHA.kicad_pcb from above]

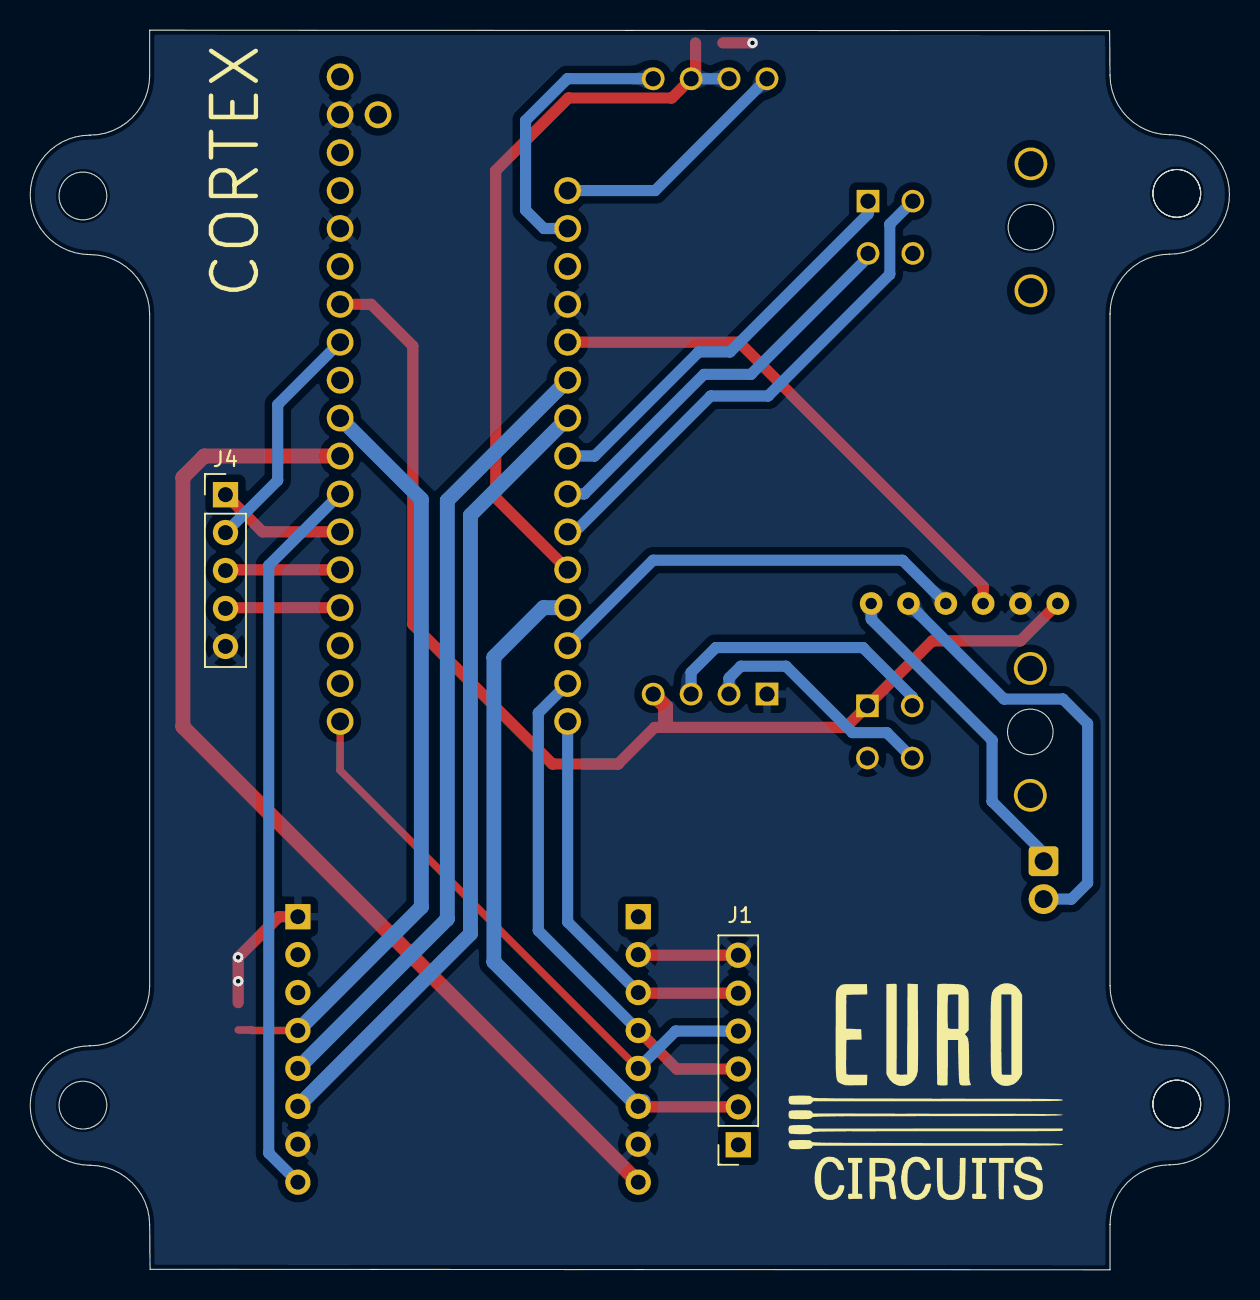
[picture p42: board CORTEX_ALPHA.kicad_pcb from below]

Board: 2 copper layers, 80.3 x 83.0 mm, 11 parts (2 on the bottom side), 28 nets.

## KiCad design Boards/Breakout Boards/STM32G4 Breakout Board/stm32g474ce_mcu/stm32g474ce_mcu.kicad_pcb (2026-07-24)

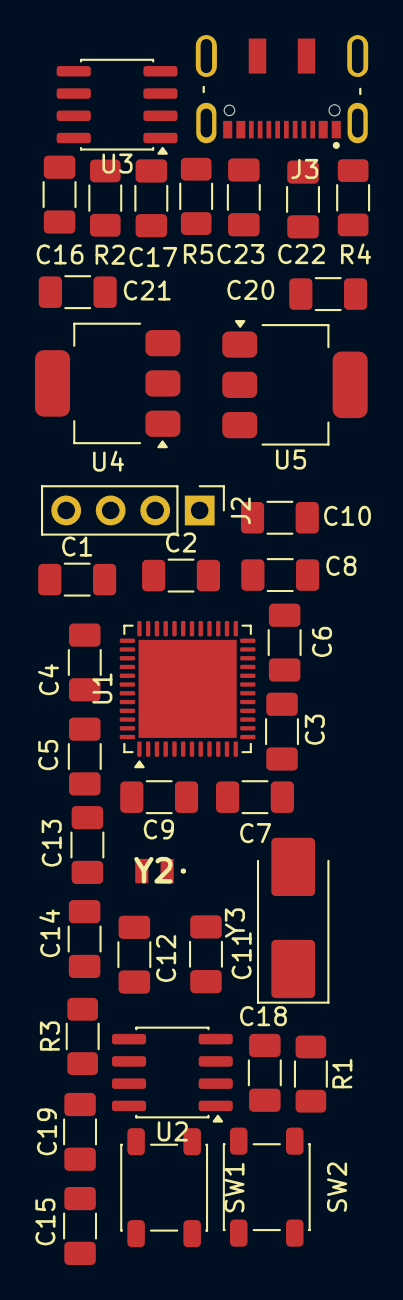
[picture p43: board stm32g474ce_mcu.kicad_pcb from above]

Board: 2 copper layers, 39 parts (0 on the bottom side), 21 nets, no tracks yet.

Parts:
C1, C2, C3, C5, C8: 100n; C_1206_3216Metric_Pad1.33x1.80mm_HandSolder
C4: 4.7u; C_1206_3216Metric_Pad1.33x1.80mm_HandSolder
C6: 10n; C_1206_3216Metric_Pad1.33x1.80mm_HandSolder
C7, C9, C10: 1u; C_1206_3216Metric_Pad1.33x1.80mm_HandSolder
C11, C12: 9p; C_1206_3216Metric_Pad1.33x1.80mm_HandSolder
C13, C14: 3.5p; C_1206_3216Metric_Pad1.33x1.80mm_HandSolder
C15, C16, C17, C18, C19: 0.1u; C_1206_3216Metric_Pad1.33x1.80mm_HandSolder
C20, C22: 10u; C_1206_3216Metric_Pad1.33x1.80mm_HandSolder
C21: 22u; C_1206_3216Metric_Pad1.33x1.80mm_HandSolder
C23: 28u; C_1206_3216Metric_Pad1.33x1.80mm_HandSolder
J2: Conn_01x04_Pin; PinHeader_1x04_P2.54mm_Vertical
J3: DX07S016JA1R1500; JAE_DX07S016JA1R1500
R1: 10k; R_1206_3216Metric_Pad1.30x1.75mm_HandSolder
R2, R3: 120; R_1206_3216Metric_Pad1.30x1.75mm_HandSolder
R4, R5: 5k1; R_1206_3216Metric_Pad1.30x1.75mm_HandSolder
SW1: RESET; SW_SPST_PTS647_Sx38
SW2: SW_SPDT; SW_SPST_PTS647_Sx38
U1: STM32G473CEUx; QFN-48-1EP_7x7mm_P0.5mm_EP5.6x5.6mm
U2, U3: MCP2562FDT; SOIC-8_3.9x4.9mm_P1.27mm
U4: AMS1117-3.3; SOT-223-3_TabPin2
U5: AMS1117-5.0; SOT-223-3_TabPin2
Y2: 3.768k; ABS06-32Khz
Y3: 8Mhz; Crystal_SMD_0603-2Pin_6.0x3.5mm_HandSoldering

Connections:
+3.3V: C1.1, C2.1, C3.1, C4.1, C5.1, C6.1, C7.1, C8.1, C9.1, C10.1, C16.2, C19.2, C21.1, J2.1, U1.1 (VBAT), U1.20 (VREF+), U1.21 (VDDA), U1.23 (VDD), U1.35 (VDD), U1.48 (VDD), U2.5 (Vio), U3.5 (Vio), U4.2 (VO)
+5V: C17.1, C18.1, C20.1, C23.1, U2.3 (VDD), U3.3 (VDD), U4.3 (VI), U5.2 (VO)
/BOOT0: R1.2, U1.46 (PB8)
/OSC32_IN: C14.2, U1.3 (PC14), Y2.2
/OSC32_OUT: C13.2, U1.4 (PC15), Y2.1
/OSC_IN: C11.2, U1.5 (PF0), Y3.2
/OSC_OUT: C12.2, U1.6 (PF1), Y3.1
/SWCLK: J2.3, U1.37 (PA14)
/SWDIO: J2.2, U1.36 (PA13)
FDCAN2_RX: U1.43 (PB5), U3.4 (RXD)
FDCAN2_TX: U1.44 (PB6), U3.1 (TXD)
FDCAN3_RX: U1.41 (PB3), U2.4 (RXD)
FDCAN3_TX: U1.42 (PB4), U2.1 (TXD)
GND: C1.2, C2.2, C3.2, C4.2, C5.2, C6.2, C7.2, C8.2, C9.2, C10.2, C11.1, C12.1, C13.1, C14.1, C15.2, C16.1, C17.2, C18.2, C19.1, C20.2, C21.2, C22.2, C23.2, J2.4, J3.1 (GND), J3.12 (GND), R4.1, R5.1, SW1.2, SW2.1 (A), U1.49 (VSS), U2.2 (VSS), U2.8 (STBY), U3.2 (VSS), U3.8 (STBY), U4.1 (GND), U5.1 (GND)
NRST: C15.1, SW1.1, U1.7 (PG10)
unnamed: J3.3 (CC1), R4.2
unnamed: J3.9 (CC2), R5.2
unnamed: R1.1, SW2.2 (B)
USB_D+: J3.6 (D+), J3.7 (D+), U1.34 (PA12)
USB_D-: J3.5 (D-), J3.8 (D-), U1.33 (PA11)
VBUS: C22.1, J3.2 (VBUS), J3.11 (VBUS), U5.3 (VI)

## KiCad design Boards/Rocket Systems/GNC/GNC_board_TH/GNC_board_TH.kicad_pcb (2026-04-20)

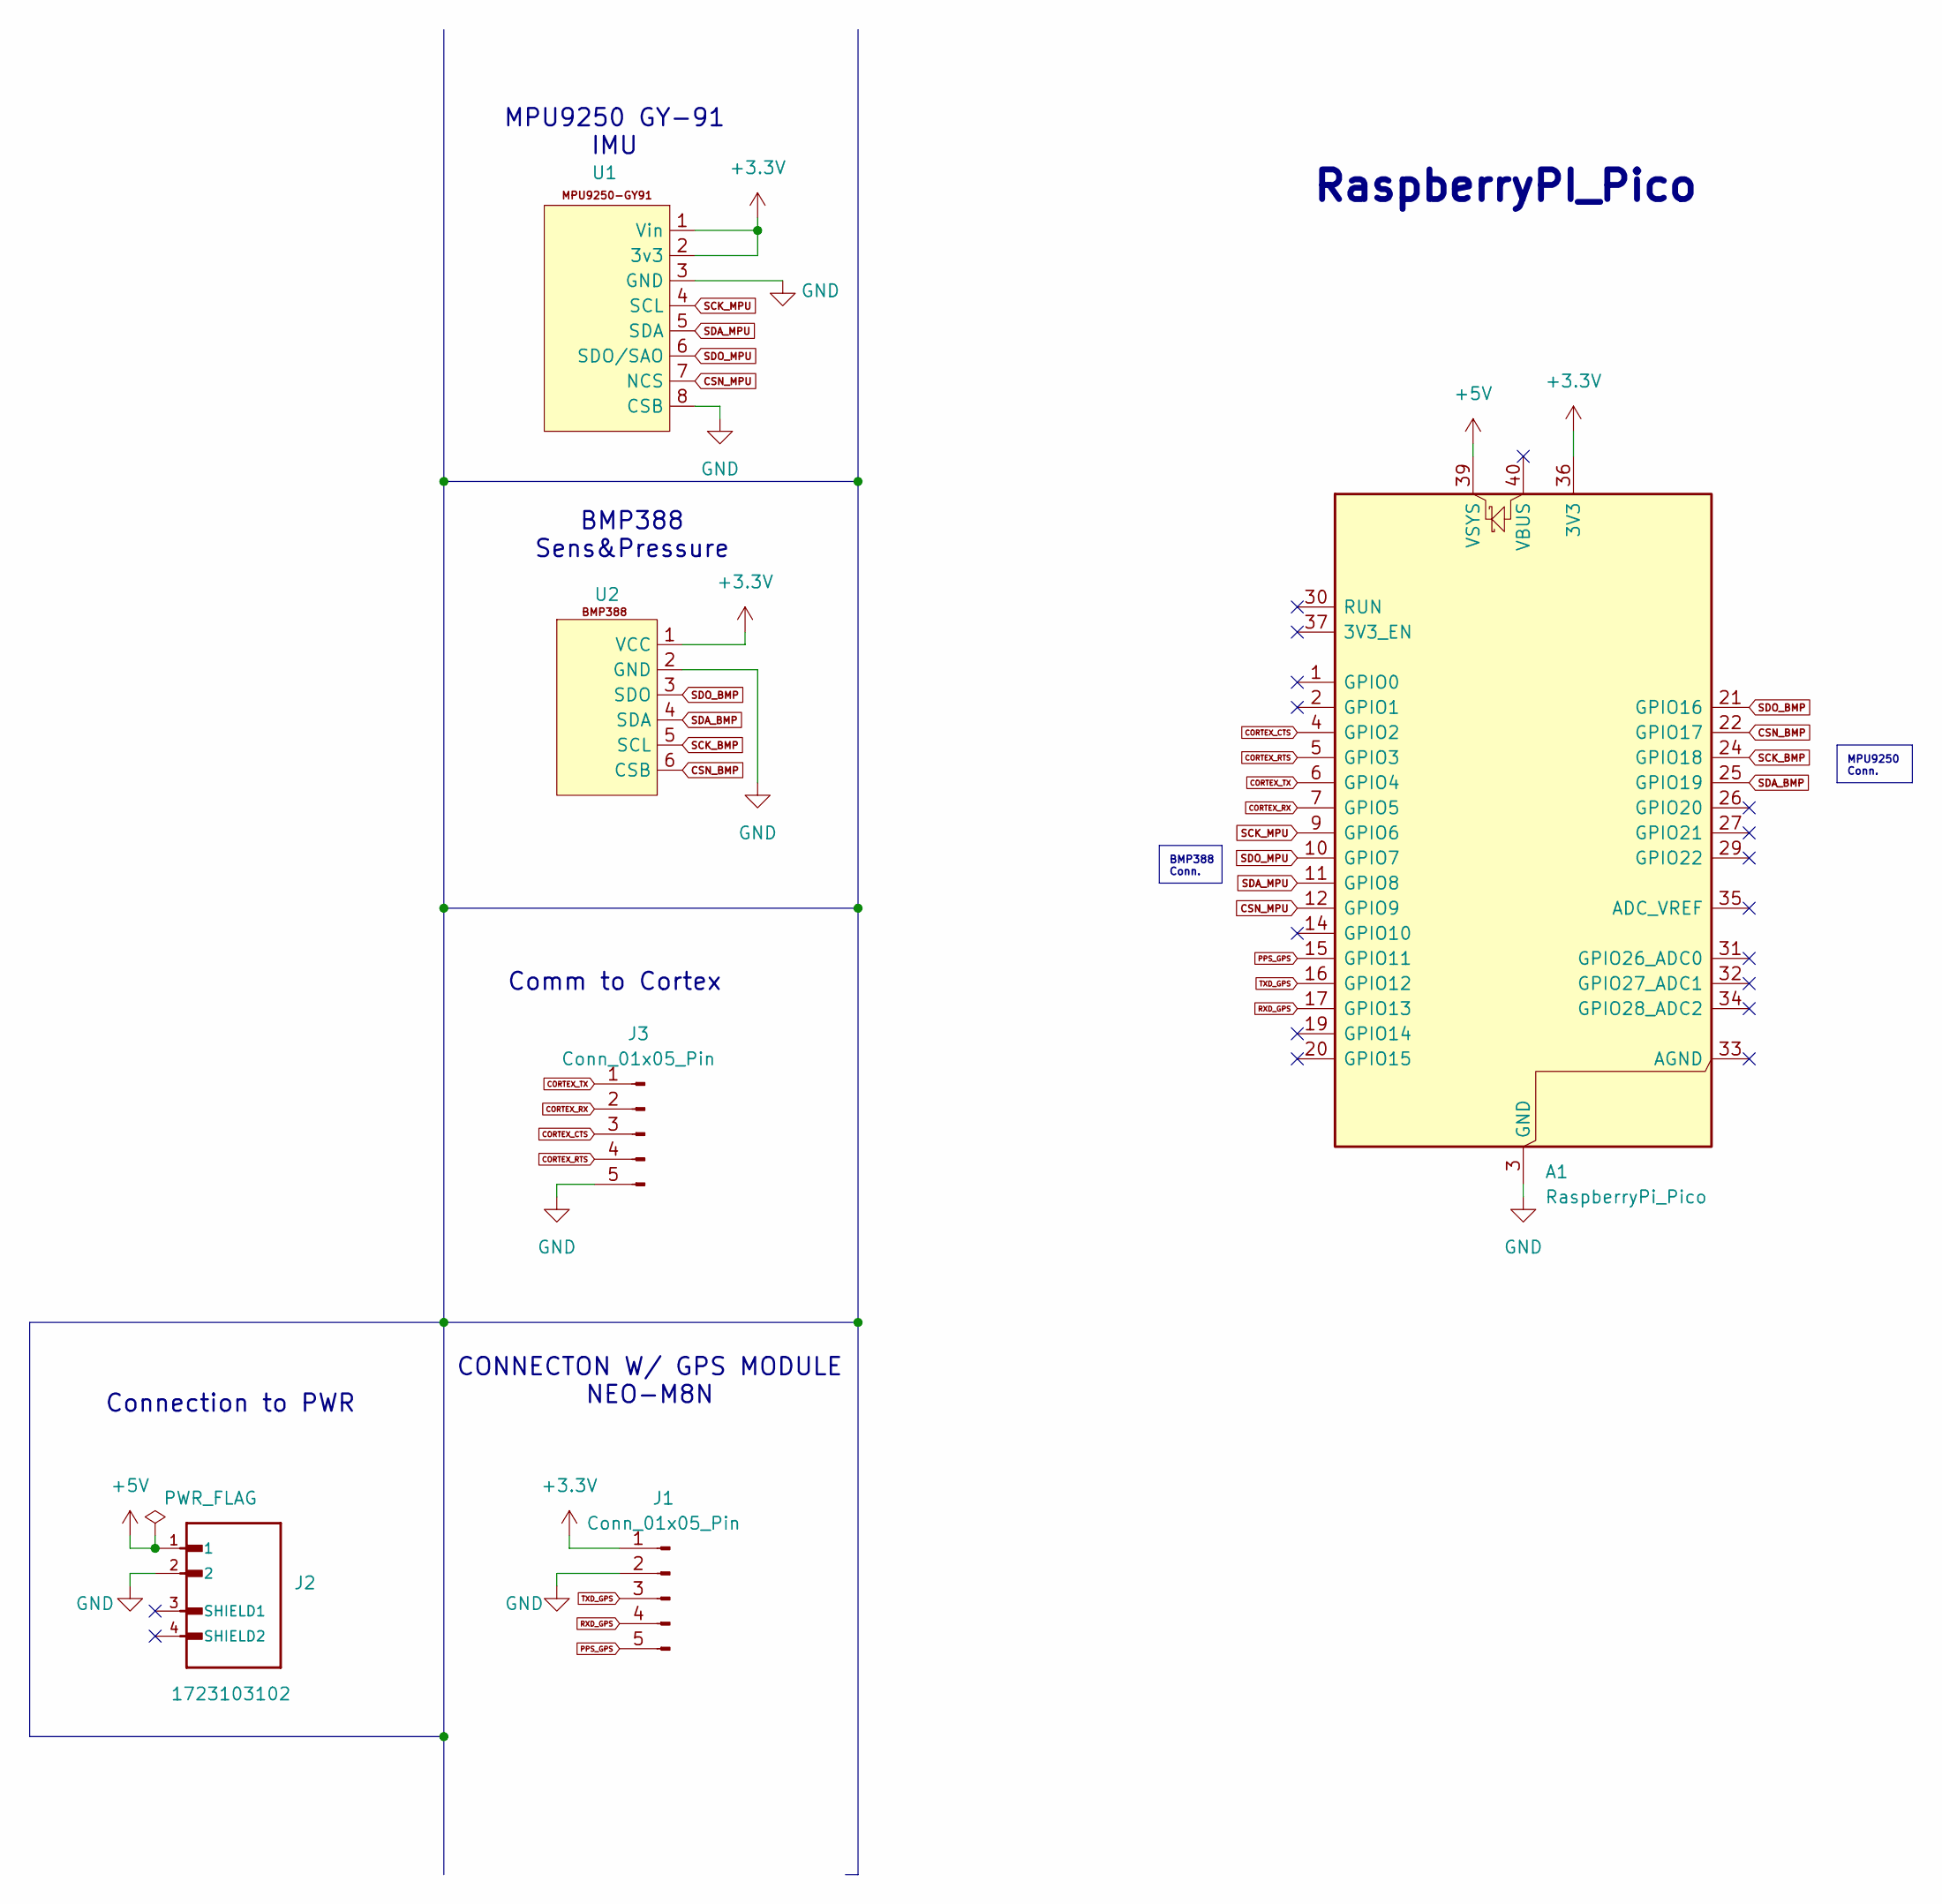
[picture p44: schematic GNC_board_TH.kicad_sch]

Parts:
A1: RaspberryPi_Pico; RaspberryPi_Pico_Common_Unspecified
J1, J3: Conn_01x05_Pin; PinSocket_1x05_P2.54mm_Vertical
J2: 1723103102; CONN02_1723103102_MOL; MANUFACTURER_PART_NUMBER 1723103102; DigiKey_Part_Number 900-1723103102-ND
U1: MPU9250
U2: BMP388

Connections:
+3.3V: A1.36 (3V3), J1.1, U1.1 (Vin), U1.2 (3v3), U2.1 (VCC)
+5V: A1.39 (VSYS), J2.1
CORTEX_CTS: A1.4 (GPIO2), J3.3
CORTEX_RTS: A1.5 (GPIO3), J3.4
CORTEX_RX: A1.7 (GPIO5), J3.2
CORTEX_TX: A1.6 (GPIO4), J3.1
CSN_BMP: A1.22 (GPIO17), U2.6 (CSB)
CSN_MPU: A1.12 (GPIO9), U1.7 (NCS)
GND: A1.3 (GND), A1.8 (GND), A1.13 (GND), A1.18 (GND), A1.23 (GND), A1.28 (GND), A1.38 (GND), J1.2, J2.2, J3.5, U1.3 (GND), U1.8 (CSB), U2.2 (GND)
PPS_GPS: A1.15 (GPIO11), J1.5
RXD_GPS: A1.17 (GPIO13), J1.4
SCK_BMP: A1.24 (GPIO18), U2.5 (SCL)
SCK_MPU: A1.9 (GPIO6), U1.4 (SCL)
SDA_BMP: A1.25 (GPIO19), U2.4 (SDA)
SDA_MPU: A1.11 (GPIO8), U1.5 (SDA)
SDO_BMP: A1.21 (GPIO16), U2.3 (SDO)
SDO_MPU: A1.10 (GPIO7), U1.6 (SDO/SAO)
TXD_GPS: A1.16 (GPIO12), J1.3

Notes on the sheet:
MPU9250 GY-91 IMU
RaspberryPI_Pico
BMP388 Sens&Pressure
CONNECTON W/ GPS MODULE NEO-M8N
Comm to Cortex
Connection to PWR
BMP388 Conn.
MPU9250 Conn.


Board: 2 copper layers, 54.1 x 64.0 mm, 6 parts (0 on the bottom side), 18 nets.

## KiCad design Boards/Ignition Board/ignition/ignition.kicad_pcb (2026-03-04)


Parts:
A1: RaspberryPi_Pico; RaspberryPi_Pico_Common_Unspecified
C7: 10uF; C_0402_1005Metric
J2: E-Match; TerminalBlock_Xinya_XY308-2.54-2P_1x02_P2.54mm_Horizontal
KEY1: Screw_Terminal_01x02; TerminalBlock_Xinya_XY308-2.54-2P_1x02_P2.54mm_Horizontal
PILHAS1: Screw_Terminal_01x02; TerminalBlock_Xinya_XY308-2.54-2P_1x02_P2.54mm_Horizontal
Q1: IRLB8721PBF; TO-220-3_Vertical
R1, R5: 10K; R_0402_1005Metric
R2: 100; R_0402_1005Metric
R3: 220; R_0402_1005Metric
R4: 330; R_0402_1005Metric
Switch1, Switch3: .; TerminalBlock_Xinya_XY308-2.54-2P_1x02_P2.54mm_Horizontal
Switch2: Screw_Terminal_01x02; TerminalBlock_Xinya_XY308-2.54-2P_1x02_P2.54mm_Horizontal
U1: E28-2G4M27SX; Radio_Module_PST
U2: DCDC_Module
U3: PC817; PC817X_SHP

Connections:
+3.3V: A1.39 (VSYS), C7.1, Switch2.2, U1.1 (VCC), U2.3 (OUT+), U3.4
/FLAG_IGNITE: A1.12 (GPIO9), R3.1, R5.1, U3.3
/LGC_IGNITE: A1.15 (GPIO11), R2.2
/RD_BUSY: A1.27 (GPIO21), U1.12 (BUSY)
/RD_DIO1: A1.26 (GPIO20), U1.13 (DIO1)
/RD_DIO2: U1.14 (DIO2)
/RD_DIO3: U1.15 (DIO3)
/RD_MISO: A1.21 (GPIO16), U1.3 (MISO_TX)
/RD_MOSI: A1.25 (GPIO19), U1.4 (MOSI_RX)
/RD_NSS: A1.22 (GPIO17), U1.6 (NSS_CTS)
/RD_RESET: A1.29 (GPIO22), U1.11 (NRESET)
/RD_RX: A1.14 (GPIO10), U1.8 (RX_EN)
/RD_SCK: A1.24 (GPIO18), U1.5 (SCK_RTSN)
/RD_TX: A1.20 (GPIO15), U1.9 (TX_EN)
/REG_IN: Switch1.2, U2.1 (IN+)
GND: A1.3 (GND), A1.8 (GND), A1.13 (GND), A1.18 (GND), A1.23 (GND), A1.28 (GND), A1.38 (GND), C7.2, Q1.3 (S), R1.1, R5.2, Switch3.1, U1.2 (GND), U1.7 (GND), U1.10 (GND), U1.16 (GND), U2.4 (OUT-), U3.2
unnamed: J2.1, Q1.2 (D)
unnamed: J2.2, KEY1.1, R4.1
unnamed: KEY1.2, Switch2.1
unnamed: PILHAS1.1, U2.2 (IN-)
unnamed: PILHAS1.2, Switch1.1
unnamed: Q1.1 (G), R1.2, R2.1
unnamed: R4.2, U3.1
unnamed: R3.2, Switch3.2

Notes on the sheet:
Ignition Circuit
Power Circuit
RADIO MODULE E28-2G4M27SX
RASPBERRY PI PICO


Board: 2 copper layers, 49.5 x 83.4 mm, 17 parts (0 on the bottom side), 22 nets.

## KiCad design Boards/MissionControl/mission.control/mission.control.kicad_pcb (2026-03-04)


Board: 2 copper layers, 81.2 x 82.6 mm, 15 parts (0 on the bottom side), 24 nets.

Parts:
A1: RaspberryPi_Pico; RaspberryPi_Pico_Common_Unspecified
AbortBtn: .; TerminalBlock_Xinya_XY308-2.54-2P_1x02_P2.54mm_Horizontal
ArmKey: .; TerminalBlock_Xinya_XY308-2.54-2P_1x02_P2.54mm_Horizontal
BZ1: Buzzer; Buzzer_TDK_PS1240P02BT_D12.2mm_H6.5mm
FireBtn: .; TerminalBlock_Xinya_XY308-2.54-2P_1x02_P2.54mm_Horizontal
Led: .; TerminalBlock_Xinya_XY308-2.54-2P_1x02_P2.54mm_Horizontal
R1: 220Ω; R_0402_1005Metric
R2: 100Ω; R_0402_1005Metric
R3, R4, R5: 10KΩ; R_0402_1005Metric
R6: 1KΩ; R_0402_1005Metric
U1: E28-2G4M27SX; Radio_Module_PST
U2: MAX485_MODULE_5V_LOGIC_TLL_TO_RS-485_CONVERTER; MODULE_MAX485_MODULE_5V_LOGIC_TLL_TO_RS-485_CONVERTER
U3: CANController

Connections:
+3.3V: A1.36 (3V3), AbortBtn.1, ArmKey.1, FireBtn.1, U1.1 (VCC)
+5V: A1.40 (VBUS), U2.4 (VCC), U3.7 (VCC1), U3.8 (VCC)
/ABORT_SIGNAL: A1.14 (GPIO10), AbortBtn.2, R4.2
/ARM_SIGNAL: A1.12 (GPIO9), ArmKey.2, R5.2
/BUZZER_SIGNAL: A1.4 (GPIO2), R2.1
/CAN_CS: A1.2 (GPIO1), U3.5 (CS)
/CAN_INT: A1.1 (GPIO0), U3.1 (INT)
/FIRE_SIGNAL: A1.15 (GPIO11), FireBtn.2, R3.2
/LED_SIGNAL: A1.11 (GPIO8), R1.2
/RADIO_BUSY: A1.20 (GPIO15), U1.12 (BUSY)
/RADIO_CS: A1.22 (GPIO17), U1.6 (NSS_CTS)
/RADIO_DIO1: A1.19 (GPIO14), U1.13 (DIO1)
/RADIO_NRESET: A1.5 (GPIO3), U1.11 (NRESET)
/RADIO_RX_EN: A1.9 (GPIO6), U1.8 (RX_EN)
/RADIO_TX_EN: A1.7 (GPIO5), U1.9 (TX_EN)
/RS_DI: A1.16 (GPIO12), U2.8 (DI)
/RS_RO: A1.17 (GPIO13), U2.5 (RO)
/RS_TXEN: A1.29 (GPIO22), R6.1, U2.6 (RE), U2.7 (DE)
/SPI0_MISO: A1.21 (GPIO16), U1.3 (MISO_TX), U3.4 (SO)
/SPI0_MOSI: A1.25 (GPIO19), U1.4 (MOSI_RX), U3.3 (SI)
/SPI0_SCK: A1.24 (GPIO18), U1.5 (SCK_RTSN), U3.2 (SCK)
GND: A1.3 (GND), A1.8 (GND), A1.13 (GND), A1.18 (GND), A1.23 (GND), A1.28 (GND), A1.38 (GND), BZ1.2 (-), Led.2, R3.1, R4.1, R5.1, R6.2, U1.2 (GND), U1.7 (GND), U1.10 (GND), U1.16 (GND), U2.1 (GND), U3.6 (GND)
unnamed: BZ1.1 (+), R2.2
unnamed: Led.1, R1.1

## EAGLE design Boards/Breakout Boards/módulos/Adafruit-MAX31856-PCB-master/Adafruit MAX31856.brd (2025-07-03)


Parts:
C1: 0.01uF; 0805_10MGAP
C2, C4, C5: 0.1uF; 0805-NO
C3: 0.01uF; 0805-NO
C6, C7: 10uF; 0805-NO
D1, D2, D3: 1N4148; SOD-323
FID1, FID2: FIDUCIAL""; FIDUCIAL_1MM
JP1: HEADER-1X970MIL; 1X09_ROUND_70
R1, R2: 100; 0805-NO
R3, R4, R5: 10K; 0805-NO
U1: mic5225-3.3; SOT23-5
U2: MAX31856; TSSOP14
U$13, U$14: MOUNTINGHOLE2.5; MOUNTINGHOLE_2.5_PLATED
X1: 3.5mm term; TERMBLOCK_1X2-3.5MM

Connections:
3.3V: C4.1, C5.1, C7.1, JP1.8, R3.2, R4.2, R5.2, U1.5 (OUT), U2.5 (AVDD), U2.8 (DVDD)
!CS: D1.C, JP1.3
!CS_3V: D1.A, R5.1, U2.9 (!CS)
!FAULT: JP1.2, U2.13 (!FAULT)
DRDY: JP1.1, U2.7 (!DRDY)
GND: C1.1, C3.2, C4.2, C5.2, C6.2, C7.2, JP1.7, U1.2 (GND), U2.1 (AGND), U2.14 (DGND)
SCK: D2.C, JP1.6
SCK_3V: D2.A, R4.1, U2.10 (SCK)
SDI: D3.C, JP1.4
SDO: JP1.5, U2.11 (SDO)
SDO_3V: D3.A, R3.1, U2.12 (SDI)
T+: C2.2, C3.1, R2.2, U2.4 (T+)
T-: C1.2, C2.1, R1.2, U2.3 (T-)
THERM+: R2.1, X1.1
THERM-: R1.1, U2.2 (BIAS), X1.2
VIN: C6.1, JP1.9, U1.1 (IN), U1.3 (EN)


Board: 2 copper layers, 24.1 x 21.6 mm, 28 parts (1 on the bottom side), 16 nets.

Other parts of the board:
U$1: PCBFEAT-REV-040
U$23: SYMBOL_PLUS
U$24: SYMBOL_MINUS
U$25: ADAFRUIT_3.5MM
U$26: ADAFRUIT_TEXT_20MM

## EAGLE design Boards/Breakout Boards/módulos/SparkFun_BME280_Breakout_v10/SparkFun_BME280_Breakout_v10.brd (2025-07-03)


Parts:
C1, C2: 0.1uF; 0603-CAP
FID1, FID2: FIDUCIAL1X2; FIDUCIAL-1X2
FRAME1: FRAME-LETTER; CREATIVE_COMMONS
JP1: I2C_STANDARD_NO_SILK; 1X04_NO_SILK
JP2: M06NO_SILK_FEMALE_PTH; 1X06_NO_SILK
LOGO1, LOGO2: SFE_LOGO_FLAME.1_INCH; SFE_LOGO_FLAME_.1
LOGO3: OSHW-LOGOS; OSHW-LOGO-S
R1, R2, R3, R4: 4.7K; 0603-RES
SJ1: EN I2C PULL; PAD-JUMPER-3-3OF3_NC_BY_TRACE_YES_SILK_FULL_BOX
SJ2: EN I2C MODE; PAD-JUMPER-2-NC_BY_TRACE_YES_SILK
SJ3: EN ADR PULLUP; PAD-JUMPER-3-2OF3_NC_BY_TRACE_YES_SILK_FULL_BOX
STANDOFF4: STAND-OFF
U1: BME280; BME280_LGA

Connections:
3.3V: C1.1, C2.1, JP1.2, JP2.5, R4.2, SJ1.2, SJ2.2, U1.P$6 (VDDIO), U1.P$8 (VDD)
!CS: JP2.1, R3.1, U1.P$2 (!CS)
GND: C1.2, C2.2, JP1.1, JP2.6, SJ3.1, U1.P$1 (GND1), U1.P$7 (GND2)
unnamed: R1.2, SJ1.3
unnamed: R2.2, SJ1.1
unnamed: R3.2, SJ2.1
unnamed: R4.1, SJ3.3
SCK/SCL: JP1.4, JP2.4, R2.1, U1.P$4 (SCK/SCL)
SDI/SDA: JP1.3, JP2.2, R1.1, U1.P$3 (SDI/SDA)
SDO/ADR: JP2.3, SJ3.2, U1.P$5 (SDO/ADR)

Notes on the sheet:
Marshall Taylor
V10
BME280 Breakout
SJ3 controls the lowest bit of the I2C address--can be: 0x1110110 0x1110111 Open for SPI 3-wire mode
SJ1 pulls up the SCK and SDA lines for I2C operation
Ports:
(Use only 1)
I2C
SPI
MODES: I2C: Leave the copper-connected jumpers SJ1-SJ2 as default, use SJ3 to set the I2C address. SPI 4-WIRE: Jumpers SJ1-SJ3 can be opened to remove 4.7k load on the SPI lines but is not necessary. SPI 3-WIRE: SJ3 must be opened.
SJ2 pulls up the !CS! line forcing I2C mode if no signal is on !CS!.



Board: 2 copper layers, 12.7 x 20.3 mm, 19 parts (4 on the bottom side), 10 nets.

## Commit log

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2024-12-29 To do list update: Comms board
    Corrigir erros do ERC e teste de sincronização do repo
    [Communication Board.kicad_sch]
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2024-12-29 Adição de Connectors
    Connector "CONN Female Header 22022065" adicionado à library
    Connectors do UART, 5V e GND adicionados à OBC
    [OBC board.kicad_pcb]
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2024-12-30 Preparação do RP2040 para PCB Design
    Foram corrigidos todos os ERC errors e warnings. Foram feitas alterações
    aos necessários simbolos, e foi adicionado um botão na biblioteca de
    simbolos
    [RP2040 Standard Design.kicad_sch, RP2040 Standard.kicad_sch, TL3305CF160QG.step]
2024-12-30 Correção de erros ERC no OBC e correção de simbolos usados
    [OBC board.kicad_sch, RP2040 Standard Design.kicad_sch]
2024-12-30 Correção de erros ERC na Communication Board
    Foram corrigidos todos os erros e avisos ERC na Communication Board.
    Foram feitas alterações aos ficheiros de alguns símbolos e adicionou-se
    um Schottky Diode de proteção
    [Communication Board.kicad_sch, PMEG2010ER.step, RP2040 Standard.kicad_sch]
2024-12-30 Algumas correções ERC e ajustes no Design dos DCDC
    [CANha Boards.kicad_sch, RP2040 Standard Design.kicad_sch, RP2040 Standard.kicad_sch]
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2025-01-01 Correção do últimos erros ERC e adição do sensor de temperatura
    Tbm revi a linha do ADC, adicionei novos simbolos incluindo um NMOS
    MOSFET e um Schottky
    [CANha Boards.kicad_sch, RP2040 Standard Design.kicad_sch, RSX301L-30DDTE25.stp]
2025-01-03 pequenas alterações, implementação do sensor de temperatura na placa de comunicações
    [CANha Boards.kicad_sch, Communication Board.kicad_sch, RP2040 Standard Design.kicad_sch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]
2025-01-09 Atualização footprints
    Footprints das resistencias, condensadores e indutores + Ferrite
    [BLM18BD601SN1D.step]
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2025-01-09 new usb-c symbol and ads1114 footprint correction
    [DX07S016JA1R1500.step]
2025-01-10 Atualizações footprints
    Adicionei a Resistência de 27 ohms que faltava na biblioteca Symbols Lib;
    Atualizei as footprints do OBC menos a componente J6;
    [OBC board.kicad_pcb, OBC board.kicad_sch, RP2040 Standard Design.kicad_sch]
2025-01-10 COMS
    Acho que já está tudo de footprints que tinha que fazer na Communication Board
    [Communication Board.kicad_pcb, Communication Board.kicad_sch, RP2040 Standard.kicad_sch]
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2025-01-11 pequenas correções em algumas resistências e bugfix do simobolo do Barometro
    [CANha Boards.kicad_sch, Communication Board.kicad_sch, OBC board.kicad_sch]
2025-01-12 bugfix do pull request merge
    [OBC board.kicad_sch]
2025-01-23 changes in RP2040 design
    GPIO25 LED is now part of RP2040 Standard
    [CANha Boards.kicad_sch, Communication Board.kicad_sch, OBC board.kicad_sch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]
2025-01-25 Reorganização da biblioteca de simbolos por categorias
    A SymbolsLib foi atualizada para estar por categorias
    [1060TR.step, DX07S016JA1R1500.step, HSMH-H191.stp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]
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2025-01-25 Green LED footprint fix
2025-01-25 Inicio de integração do RF FEM nas placas de comunicação
    [G&F COMMS.kicad_sch]
2025-01-26 Led driver circuit correction & RF FEM implementation
    [G&F COMMS.kicad_pcb, G&F COMMS.kicad_sch, NSVT30010MXV6T1G.stp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]
2025-01-27 Sockets Pico_Conn
    Adição à Library e ao RP2040 S de Sockets iguais às placas de Pico.
    [RP2040 S.kicad_pcb, RP2040 S.kicad_sch, RP2040 Standard Design.kicad_sch]
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2025-01-27 Male CONN adicionado e OBC atualizado
    - Connector macho que liga a R COMMS ao OBC adicionado à biblioteca
    - OBC com as footprints atualizadas
    [OBC.kicad_sch, RP2040 Standard Design.kicad_sch]
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2025-01-28 Footprints (RP2040 Corrigido e OBC)
    [OBC.kicad_pcb, OBC.kicad_sch, RP2040 S.kicad_pcb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]
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2025-01-30 Mudanças nas Schematics
    - Capacitor-0805 adicionado à library
    - Nomes de Passive Components atualizados na library
    - Atualizado as footprint dos RP2040 S, OBC, R COMMS
    [CL21B106KOQNNNE.step, OBC.kicad_sch, R COMMS.kicad_sch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]
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2025-02-04 USB-C PD update and schematic corrections
    [G&F COMMS.kicad_sch, OBC.kicad_sch, R COMMS.kicad_sch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]
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2025-02-11 TVCS rework
    [TVCS Fill.kicad_sch, TVCS Top.kicad_sch]
2025-02-11 TVCS pinout rework
    [HSMH-H191.stp, R COMMS.kicad_sch, TVCS Top.kicad_sch]
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2025-02-12 I2C translator symbol fix and TVCS final touches
    [PCA9306GM,125.stp, PTS060301B100RP100.stp, RP2040 Standard Design.kicad_sch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]
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2025-02-16 RP2040 S PCB (Part #1)
    Diversos crimes de guerra contra as pcbs foram cometidos com esta alteração. Ao dar merge está a compactuar com os ditos crimes e terá de confrontar as autoridades.
    [RP2040 S.kicad_pcb, RP2040 S.kicad_sch, RP2040 Standard Design.kicad_sch]
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2025-02-16 TVCS Final update (1)
    Só falta implementar LEDs de Status/maybe Buzzer
    [BC857CMB_315.step, NCR420ZX.stp, TVCS Top.kicad_sch]
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2025-02-23 Atualização RP2040 P
    Copiei da TVCS Top;
    Alterei conexões no microcontrolador;
    Tentei pôr o Potenciómetro;
    [RP2040 P.kicad_pcb, RP2040 P.kicad_sch]
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2025-03-01 RP2040 S (Part 4)
    Teste de algumas aprendizagens dos últimos tempos e inserindo as regras da EUROCIRCUITS ("BGA Component: Poolable Options")
    [RP2040 S.kicad_pcb]
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2025-03-09 commit to fix merge (1)
    [OBC.kicad_sch]
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2025-03-20 Reset PCB Payload
    [PocketStat.kicad_pcb]
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2025-03-25 RP2040S (update)
    mudar resistências de tamanho e ajustes que vieram com isso
    [RP2040 S.kicad_pcb, RP2040 Standard Design.kicad_sch]
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2025-04-06 TVCS refactor
    Muitas alterações e correções na placa TVCSO:
    Novo ADC, filtros passa baixo, novo RS transceiver, reformulação de
    conexões
    [AD8040ARUZ.step, ADS1114IDGSR.step, MAX485CSA+T.stp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]
2025-04-07 TVCS fixes and required additions
    [Power Unit.kicad_sch, Sensor Unit.kicad_sch, TVCS.kicad_sch]
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2025-04-22 first version of the routing, missing DRC rulecheck and silkscreen mapping
    [Navigator.kicad_pcb, Navigator.kicad_sch]
2025-04-24 Update PCB Payload
    Acabei o routing do ground e coloquei as camadas de GND;
    [PocketStat.kicad_pcb]
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2025-05-07 slikcreen and DRC corrections navigator
    [Navigator.kicad_pcb]
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2025-05-26 small nav and OBC updates - DFM corrections
    [Navigator.kicad_sch, OBC.kicad_pcb, OBC.kicad_sch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]
2025-05-31 OBC DFM corrections
    [OBC.kicad_pcb]
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2025-07-09 Adicionei um driver novo de leds e outras correçoes
    Adicionei um novo driver de leds substitui pelo velho e corrigimos mais
    erros de DRC
    [OBC.kicad_pcb, PocketSat.kicad_pcb, PocketSat.kicad_sch]
2025-07-09 Correção DFM JLC
    Modifiquei a PCB para passar em todos os criterios da JLC DFM
    [PocketSat.kicad_pcb]
2025-07-09 Modifiquei as footprints
    Modifiquei as footprints dos condensadores e resistencias para dar mais
    estabilidade.
    [PocketSat.kicad_pcb]
2025-07-09 mudanca na solder expansion
    mudei a solder expansion de alguma footprints do pocketsat para se
    encaixarem com as regras da DFM da JLCPCB
    [PocketSat.kicad_pcb]
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2025-07-12 PocketSat small fixes
    [PocketSat.kicad_pcb]
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2025-07-13 elytra fix
    [Elytra.kicad_sch]
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2025-07-17 Inicio da PCB Elytra
    Tive um problema com algumas footprints, tive de recomecar a pcb
    [Elytra.kicad_pcb]
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2025-07-24 OBC Final Update - DFM corrections
    [Navigator.kicad_pcb, Navigator.kicad_sch, OBC BOM - Fab File.xlsx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]
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2025-07-26 Navigator Final Update - DFM corrections
    [Elytra.kicad_sch, MMBT3906-7-F.step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]
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2025-08-02 OBC, Nav, PocketSat review - SPI and I2C mistakes corrected
    [Avionics PCBs BOM - Navigator.csv, Avionics PCBs BOM - OBC.csv, DEF0008A.stp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]
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2025-08-03 major changes on the HYDRA schematic including valve actuation and adc changes
    [Actuation Unit.kicad_sch, DDA0008D.stp, HYDRA.kicad_sch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]
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2025-08-10 corrected some ERC and changed the Connector
    [DPAK_BP-E34W_VIS.step, Elytra.kicad_pcb, Elytra.kicad_sch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]
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2025-08-15 HYDRA schematic update, ELYTRA FULL REWORK
    [Cap-8mm-THT.stp, Capacitor-6.3mm-THT.stp, Elytra.kicad_pcb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]
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2025-12-06 PCB Loadcell
    Acabei a PCB Loadcell ( Disposto a mudanças). Vai ser reviewed pelo Alexandre.
    [393570004.stp, Load_cell.kicad_pcb, Load_cell.kicad_sch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]
2025-12-08 PCB Loadcells Acabada
    Acabei o design das pcbs das loadcells, so falta colocar os logos e buracos m3.
    [LIFT.kicad_pcb, LIFT.kicad_sch, Load_cell.kicad_pcb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]
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2026-01-12 PCB LIFT CAN BUS
    adicionei um controlador de can para futuras implementaçoes
    [393570002.stp, LIFT.kicad_pcb, LIFT.kicad_sch]
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2026-05-17 PMU
    Troca de DC DC e adição de algum labeling que faltava
    [PMU.kicad_pcb, PMU.kicad_sch]
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

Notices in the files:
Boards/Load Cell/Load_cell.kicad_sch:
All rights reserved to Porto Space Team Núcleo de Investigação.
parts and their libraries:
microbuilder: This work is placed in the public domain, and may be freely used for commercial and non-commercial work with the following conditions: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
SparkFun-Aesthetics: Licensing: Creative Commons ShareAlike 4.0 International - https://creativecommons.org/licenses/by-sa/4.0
